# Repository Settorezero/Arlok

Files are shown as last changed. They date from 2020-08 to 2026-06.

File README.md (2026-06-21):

# Arlok

## Arduino Robot you can 3D-print it yourself!

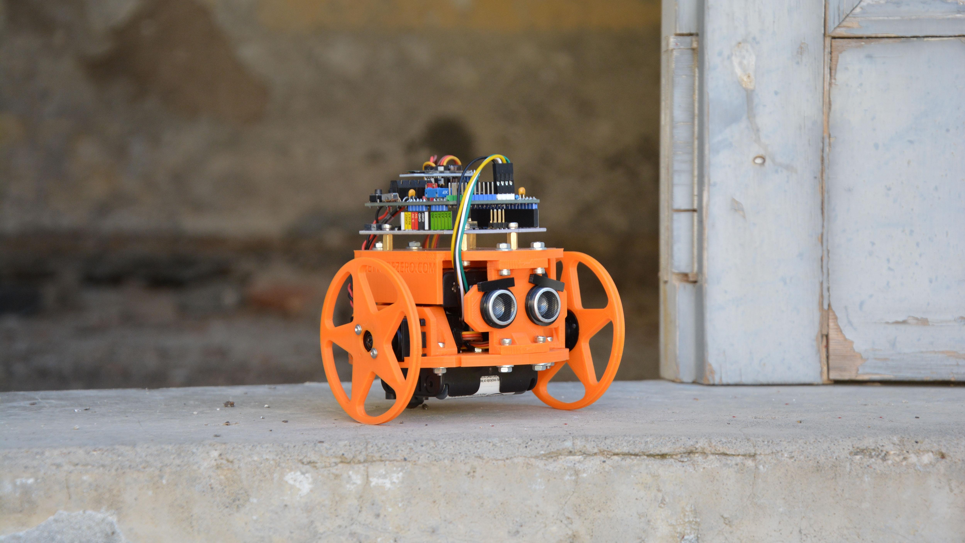
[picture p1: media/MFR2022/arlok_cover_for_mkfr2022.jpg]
Arlok - Maker Faire 2022


Arlok is a simple educational Robot based on Arduino Uno with parts printed in 3D and all easy-available components. 3D-printed parts are big, easy to manipulate and printed even by cheap 3D-printers. Arlok is highly customizable: you can change wheels and tires, supports, powering systems and give Arlok an expression too! Arlok is cheap, cute and easy to assemble and program. There are some programming examples that will make this robot moving around avoiding obstacles, following a line on the floor or let you control it using your cellphone with an Android app (source code of app provided too!).  

## What you need for build an Arlok

- Bill Of Materials: [[:uk: ENG](./docs/BOM.md)]   [[:it: ITA](./docs/BOM_ita.md)] 
- [3D-printed parts (version 1)](./cad/v1)
- [3D-printed parts (version 2 - still preliminary)](./cad/v2)

Please note: version 1 and version 2 parts are not compatible each other!  

## Version 1 vs Version 2

First Arlok version is from 2020: it was designed during Covid-19 pandemy (the very first version of the robot was called AR.L.O.). At ther time I used Tinkercad that allowed me to teach something new to my sons during the lockdown. In 2024 I started to design a new version using OnShape by PTC, mantaining the same concept design and adding some features such like a battery display and a new kind of ball-caster, but the 3D printer I had at time didn't allowed me to make some things I had in my mind. In 2025 I bought a new 3D-printer so I started to design the new version more seriously. Version 2 is here but is still a preliminary version: I added the final STEP and STL files but actually I hadn't much time for writing an assemblying tutorial like I done for the first ARLOK revision.  

Differencies between version 1 and version 2:

- The Tamiya 70144 ball-caster is no longer needed: I designed a foot for using a classic 2.5x4.5 furniture ball-caster you can find on Amazon: [sponsored link](https://amzn.to/42y9IiS). Anyway the Tamiya Ball-Caster can be used if you already have it but you must print a simple adapter you can find in both stl and step folders
- Wheels are slightly bigger and larger and are made for using only TPU printed tires: so no o-rings are needed but you need to know how to properly print TPU on your 3D-printer
- Different design for all parts: sonar and switch pillars now are larger and they cover the empty spaces giving a cleaner appearance
- Redesigned the whole chassis with the usage of a single 18650 LiPo cell in mind so, in the V2 there is no room for AA-size battery holders
- Added the possibility to use 2 18650 in parallel using the bracket for dual batteries
- Added an 1S battery display on a side
- Added a proper placement for the TP4056 (protected) 1S battery charger (tested both micro-usb and usb-c types)
- Added a proper placement for the SX1308 boost converter
- Added placement for an XL6009 boost converter (also for the XL6019 but this one cannot be used since it requires an higher input voltage, 5V)
- Added the possibility to use an VL53L0X TOF sensor instead of ultrasonic one
- Changed dimensions for allowing to use screws that will not pop-up from panels
- Changed placement of some parts for giving Arlok more stability
- Added groves for embedding nuts in some points
- Added holes and slots in certain points for passing cables in a cleaner way
- Added vent-holes for servos and boost converters
- Added handles on top for carrying Arlok more safely
- Added a further plate on top of the handles for having more expansion possibilities: plates allows the positioning of a 400-points breadboard (82x55 like this: [sponsored link](https://amzn.to/4uJOeeZ))
- Added a pedestal: you can leave Arlok on top of this pedestal for making maintenance/tuning/upgrade or simpy for showing it or allowing it to rest...

## Assembling

The Version 1 has a step-by-step guide assembly guide: [[:uk: ENG](./docs/assembly_v1.md)] - [[:it: ITA](./docs/assembly_ita_v1.md)]  
The Version 2 still doesn't have an assembly guide

## Code examples

See in the [Arduino folder](./arduino) for code examples or write your own code using one of the provided example as base!

## Mods and Upgrades

- Powering Arlok V1 from a LiPo Battery: [[:uk: ENG](./docs/lipo_mod.md)]  [[:it: ITA](./docs/lipo_mod_ita.md)] (Arlok V2 can be only powered from a LiPo)
- Hacking an analog servo for continuous rotation: [[:uk: ENG](./docs/servo_mod.md)]  [[:it: ITA](./docs/servo_mod_ita.md)]

## Troubleshooting

[Troubleshooting guide](./docs/troubleshooting.md)  

## Links

- [Greta Galli review](https://www.youtube.com/watch?v=CbPGWd9I_mA)

- [Dario Ciceri review](https://youtu.be/yjnFxoAIeAM?list=LL&t=208)

- [Aperitech about ARLO (first ARLOK rev)](https://www.youtube.com/watch?v=JS_QYEIMfNo)

- [All ARLOK videos on Youtube](https://tinyurl.com/arlokplaylist) 

- ARLOK on no. 253 (2021) of Italian Magazine "Elettronica IN": [EXCERPT](https://www.elettronicain.it/wp-content/uploads/prog_copertina/arlook_il_robot_per_tutti.pdf) -   [MAGAZINE ISSUE](https://www.elettronicain.it/prodotto/n-253-aprile-2021/?tracking=5f004a6ba8be7)

- Maker Faire 2022 [Interview by "uno scemo qualunque"](https://www.youtube.com/watch?v=RNEsY1jSlT4&t=576s)

- ARLOK partecipated to the 2020 Maker Faire European Edition (Project 253, Stand E57) - with Officine Robotiche

- ARLOK partecipated to the 2022 Maker Faire European Edition (Project 93, Pavillon D19) - with Pizza Robotics

- ARLOK partecipated to the 2023 Maker Faire European Edition (Project E62, Pavillon 5, Booth D6) - with Pizza Robotics

- ARLOK v2 partecipated to the [2026 Maker Faire Caserta](https://caserta.makerfaire.com/maker/entry/12/) (Project 12, Stand D7)

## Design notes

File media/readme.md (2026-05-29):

# Arlok (v1) Images and Renderings

- [Assembly](arlok_3d_view.stl)
- [Exploded View](arlok_3d_exploded.stl)
- [Arlok Press High Res Pictures](https://photos.app.goo.gl/kQAZxSGqNprd3ggg6)

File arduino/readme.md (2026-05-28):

# Arlok Source Code for Arduino IDE

This folder contains Arduino sketches to be used with [Arduino IDE](https://www.arduino.cc/en/main/software) after installing libraries showed in the next paragraph

> Note: The [motors setup procedure](motors_setup.md) it's only implemented in the `explorer` and `explorer lipo` sketches.

## Libraries

You'll need the following libraries installable directly from Arduino IDE otherwise specified

- [Adafruit SSD1306](https://github.com/adafruit/Adafruit_SSD1306)
- [Adafruit GFX](https://github.com/adafruit/Adafruit-GFX-Library)
- [TimerOne](https://github.com/PaulStoffregen/TimerOne) 
- [Servo Timer 2](https://github.com/nabontra/ServoTimer2) - (manual install)
- [VL53L0XV2 by Pololu](https://github.com/pololu/vl53l0x-arduino)
- [U8G2](https://github.com/olikraus/u8g2)
- [Huskylens](https://github.com/HuskyLens/HUSKYLENSArduino/tree/master) - (manual install)

## Arduino IDE Setup

Even if you're using the [MakerUNO](https://makeruno.com.my/) or other Arduino UNO compatible boards, simply select _Arduino UNO_ from the board manager. Then select the correct COM port.

## Code examples

- [Explorer](./01_Explorer) : Arlok moves around avoiding obstacles detected with ultrasonic sensor
- [Explorer TOF](./02_Explorer_TOF) : Arlok moves around avoiding obstacles detected with a VL53L0XV2 TOF Sensor (requires the V2 chassis)
- [Line Follower](./03_Linefollower) : Arlok moves following a line painted on the ground
- [Bluetooth Remote](./04_Bluetooth_Remote) : You move Arlok using Bluetooth Classic with an Android phone. Source code for Android app provided too
- [Huskyklens](./05_Huskylens) : Arlok will follow a face using an Huskylens from DFRobot

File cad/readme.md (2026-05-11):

# Arlok Files for 3D printing

- [V1](./v1) folder contains version 1 files, designed with thinkercad
- [V2](./v2) folder contains version 2 files, designed with onshape. This is still a preliminary version

PLEASE NOTE: version 1 and version 2 are not compatible each other since they've different dimensions!

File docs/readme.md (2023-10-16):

## Arlok Documents  

In this folder are contained useful documents for working with ARLOK Arduino Robot.

- [Bill of Materials](BOM.md)
- Assembly instructions: [ENG](assembly.md) - [ITA](assembly_ita.md)
- How to hack Servo for continuous rotation: [ENG](servo_mod.md) - [ITA](servo_mod_ita.md)
- [Connection table](connections.md)
- [Arlok shield schematic](arlok_schematic_rev1.png)
- Different ways to powering Arlok : [ENG](powering.md)
- Mod: Powering from a LiPo Battery: [ENG](lipo_mod.md) - [ITA](lipo_mod_ita.md)

Datasheets and manuals from product manufacturers (folder datasheet)
- [Maker UNO schematic](schematic_maker_uno.pdf)
- [Maker Line datasheet](makerline.pdf)
- [Arduino UNO schematic (only for reference)](schematic_arduino_uno.pdf)
- [HC-06 Bluetooth Module manual](HC-06_manual.pdf)
- [HC-05 AT commands](HC-05_AT_commands.pdf)
- [HC-05/06 module series](HC-0x_module_series.pdf)

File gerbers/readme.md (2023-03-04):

# Arlok PCB Gerbers (REV 1)
  
This folder contains gerber files for lastest version (REV1) PCB manufacturing. You can preview them using a free Gerber Viewer such as [GerbV](http://gerbv.geda-project.org/).  
I advice you to let PCBWay make the PCBs for you since they already have those files, without the need for you to upload and set an order.

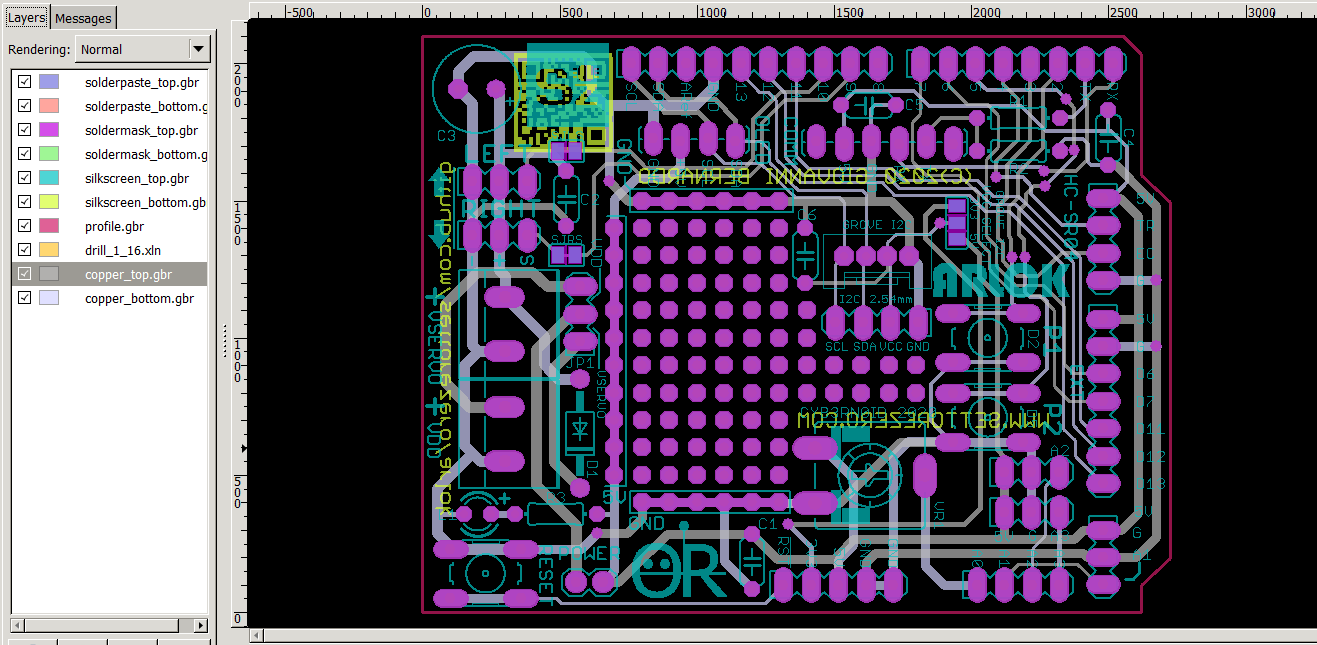
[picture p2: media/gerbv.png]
ARLOK Gerbers in GerbV


## How make ARLOK REV1 PCBs on PCBWay

- Register to PCBWay using [my refferer link](https://www.pcbway.com/setinvite.aspx?inviteid=355653&from=settorezero2020)
- Upon you registered, go to the [PCBWay ARLOK shared project page](https://www.pcbway.com/project/shareproject/ARLOK_Arduino_Shield_Rev_1_ad0b448d.html)
- Click on "Add to Cart" button on the right
- A pop-up will show up: all default settings are good. You must only select how many PCBs you want: the minimum quantity, by default, is 5. The first order of 5 PCBs is free on PCBWay: you must pay only the shipping costs

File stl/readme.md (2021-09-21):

# Arlok 3D Files for 3d-Printing 
This folder contains parts to be 3D-printed.  I like to use the [Sunlu PLA+](https://amzn.to/3aG5V7i) filament.  
> Quick link to this page: [https://tinyurl.com/3dprintarlok](https://tinyurl.com/3dprintarlok)  

## Summary
+ [Printer settings](#printersettings)
+ [Main Parts](#mainparts) 
+ [Main Parts description and notes](#descriptions)
   1. [Plate bottom](#platebottom)
   2. [Plate top](#platetop)
   3. [Servo brackets](#servobrackets)
   4. [Sonar pillar](#sonarpillar)
   5. [Rear pillar](#rearpillar)
   6. [Wheels](#wheels)
   7. [Tires](#tires)
   8. [Via Pixetto support](#viapixetto)
   9. [18650 cell bracket](#18650)
+ [How customize the wheels](#customizewheels) 
+ [Moods](#moods)

## Printer settings
Values in the parts table are calculated using CURA slicer with following settings:

- Layer Height: 0.2mm
- Top Layers: 5
- Bottom Layers: 5
- Wall line count: 3
- Print speed: 30mm/sec
- Infill speed: 50mm/sec
- Travel speed: 65mm/sec
- Infill density: 20%
- Generate Support: NO
- Build plate adhesion type: skirt

I use those slow settings because I've a cheap 3D-Printer and I need to print slow. Also Infill maybe is slightly oversized since pieces are pretty big. If you've a good 3D-printer you can speed-up and lower the infill.

## Main Parts
You can see the [Arlok Exploded View](../media/arlok_3d_exploded.stl) for seeing how parts must be assembled.  
Part quantity in parenthesis indicates that this is an optional or an alternative part.  
Time and weight is reported for total parts if more than one is needed.

| Qt. | File | Print Time (minutes) | Weight (grams)| Notes |
|-----|---|---|---|---|
|  1  | [Plate Bottom](arlok_plate_bottom.stl) | 199 | 26 |  |
|  1  | [Plate Top](arlok_plate_top.stl) | 216 | 30 |  |
|  2  | [Servo Bracket](arlok_servo_bracket.stl) | 106 | 12 |  |
|  1  | [Sonar Pillar](arlok_pillar_sonar.stl) |  48 |  6 |  |
| (1) | [Sonar Pillar (round variant)](arlok_pillar_sonar_(variant_rounded).stl) |  48 |  6 |  |
| (1) | [6mm hole Rear Pillar](arlok_pillar_hole_(variant_06mm).stl) |  40 |  6 |  | 
|  1  | [10mm hole Rear Pillar](arlok_pillar_hole_(variant_10mm).stl) |  40 |  5 |  |
| (1) | [12mm hole Rear Pillar](arlok_pillar_hole_(variant_12mm).stl) |  40 |  5 |  |
|  2  | [Wheel](arlok_wheel.stl) | 178 | 28 |  |
| (2) | [Wheel - slotted holes](./wheels/arlok_wheel_slotted.stl) | | |  |
| (2) | [Wheel - 5-star](./wheels/arlok_wheel_star5.stl) | | |  |
| (2) | [Wheel - 10-star](./wheels/arlok_wheel_star10.stl) | | |  |
| (2) | [Wheel - honeycomb](./wheels/arlok_wheel_honeycomb.stl) | | |  |
| (2) | [Wheel - circles](./wheels/arlok_wheel_circles.stl) | | |  |
| (2) | [Wheel - snowflake](./wheels/arlok_wheel_snowflake.stl) | | |  |
| (2) | [Tire - round profile](./tires/arlok_tire_round.stl) | | | See descriptions |
| (2) | [Tire - flat profile](./tires/arlok_tire_flat.stl) | | |  |
| (2) | [Tire - knurled](./tires/arlok_tire_knurled.stl) | | |  |
| (1) | [Via Pixetto Support](arlok_via_pixetto_support.stl) |  53 |  6 |  |
| (1) | [18650 LiPo Holder](arlok_18650_holder.stl) | | |  |
| ( ) | [Moods](./moods/) | | |  |

Estimated total printing time for standard parts: 13H 7'  
Estimated total filament needed for standard parts: 107g (about 36meters)

## Main Parts description and notes

### Plate Bottom
Front side is the one with the arrow on top. On front side there are two slotted holes: they are used, eventually, for attaching the Cytron Makerline module used for the line follower example. Servos must be mounted on top placing them in the grooves and having the shaft towards the front.

### Plate Top
You'll mount the Maker UNO board on top using 4 8mm or 10mm spacers. The two lateral wings will hold the 4AA battery holder in place.

### Servo Brackets
Bracket to hold in place the 2 servos: there is no need to attach servo to the bracket with screws even there are holes (they're placed there only for reference).

### Sonar Pillar
There are 2 variants: the standard, having squared edges, and the one with rounded edges, print only one of these.

### Rear Pillar
There are 3 variants that differs for the hole diameter used for the switch that detaches the 4AA batteries of the servo power. Print only 1 of these. 6mm variant will be used for the classic lever switch. 10mm variant is used for the 10mm lock pushbuttons. 12mm variant is used for the 12mm lock pushbuttons sold by FuturaShop (see [BOM in the docs folder](../docs/BOM.md)).

### Wheels
There are various kind of wheels optimized to be used with the round horn that comes with the MG996R servo and for an O-ring (or provided tires to be 3D-printed) having an internal diameter of 70mm and a section of about 2 or 3mm. Wheels are sized for giving the correct balance of the robot using the Tamiya 70144 ball caster mounted in the 25mm variant. The wheels will be attached to the servo Horns using 2 self-tapping screws given with the servos. A rubber O-Ring or a provided tire (3D printed using a flexible material like TPU) will be applied to the wheel groove for giving grip. 

The are:  
- The first, original [Wheel](./wheels/arlok_wheel.stl), see the [How customize the standard wheel](#customizewheels) for further informations
- [Wheel - slotted holes](./wheels/arlok_wheel_slotted.stl) designed by @gbr1 ([picture](../media/misc/wheel_slotted.jpg))
- [wheel - 5-star pattern](./wheels/arlok_wheel_star5.stl) designed by @gbr1
- [wheel - 10-star pattern](./wheels/arlok_wheel_star10.stl) designed by @gbr1
- [Wheel - honeycomb pattern](./wheels/arlok_wheel_honeycomb.stl) designed by @gbr1
- [Wheel - circles](./wheels/arlok_wheel_circles.stl)
- [Wheel - snowflake](./wheels/arlok_wheel_snowflake.stl)

### <a name="tires">Tires
You can use an O-ring having an internal diameter of 70mm and a section of about 2 or 3mm or, if your printer can handle flexible filaments (like TPU), you can print one of those provided tires: 

- [Tire - round profile](./tires/arlok_tire_round.stl) designed by @rbonghi (picture [[1]](../media/misc/tire_round_01.jpg) [[2]](../media/misc/tire_round_02.jpg))
- [Tire - flat profile](./tires/arlok_tire_flat.stl) designed by @gbr1
- [Tire - knurled](./tires/arlok_tire_knurled-stl) designed by @Dario-Ciceri

>@rbonghi advices those settings for the tire:
>- Filament: TPU SainSmart
>- Infill Density: 5%
>- Infill pattern: Honeycomb
>- Retraction: Disabled
>- Temperature Nozzle: 235 - 230
>- Temperature Bed: 45 - 40

###  Via Pixetto support
This support is used for attaching a [Via Pixetto Ai Camera](https://pixetto.ai/) on top-front of Arlok. The support is a hinge made of 2 pieces: you must use a long M3 screw and a nut. In the STL there are also 4 small spacers used for distancing the camera from the base: you must use M2 screws and nuts. Sorry but Via Pixetto example is still not ready.

###  18650 LiPo Holder
This part is used for holding a 18650 cell battery on the bottom of the robot. The 18650 will be used alone, without the two AA battery holders. You can use a single 18650 attached to a DC/DC boost converter through the pushbutton switch mounted on the rear pillar. Use a 18650 having soldering tabs. 

>**!!! WARNING !!!**  
**LiPo batteries can be very dangerous so don't mount this kind of battery if Arlok will be used by a child!**
  
I've successfully used a 2A DC/DC boost converter based on the [SX1308](https://amzn.to/3y07eIX). Set the converter for giving 6V at output, then feed the 6V in the `VSERVO` screw terminal and put the `JP1` jumper in `VSERVO` position and leave ON the `POWER` jumper/switch on the PCB: the main power will be disconnected through the pushbutton on the rear pillar.  

The LiPo must not go under a certain voltage so you can feed the positive terminal of the LiPo battery directly in one free analog input (`A2` for example) for checking the battery voltage and stop the robot if voltage goes below 3.2V.  
  
With those modifications the logic will be powered at about 5.3V (the 6V from the boost converter will be scaled down of about 0.7V by the voltage drop caused by `D1` diode), so for checking analog voltages keep in mind that the value `1023` from the ADC will be equal to about 5.3V (measure the precise voltage on the 5V pads and make computations accordly).  
  
This picture shows how 18650 will be mounted on the bottom of Arlok (use 2x M3 12mm screws, 2x M3 nuts and 2x M3 washers):

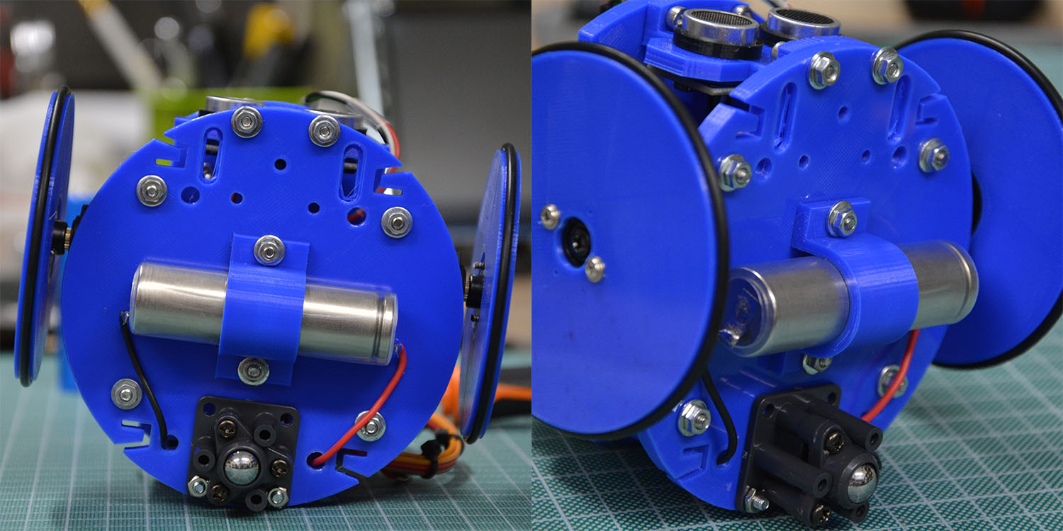
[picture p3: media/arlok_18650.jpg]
18650 LiPo battery mounting


For recharing the battery you can use a cheap module for LiPo Charging having battery protection (mandatory!), such as [this kind of module](https://amzn.to/3qjoea8) based on the `TP4056`. Module with protection are slightly larger of the ones without protection and have an additional IC on top: so be sure to buy the type having protection! It's not adviced include the battery charged on the robot: better solder two wires with crocodile-clamps on charging module and attach it to battery tabs having care robot is turned off.
  
The SX1308 module will be placed inside the robot since there is a lot of space where the 4xAA battery holder would be.  
   
If you experience some problems like reset of the Arduino, you can increase the `C3` value. If you experience bluetooth module reset, increase the value of C5 or put an electrolytic capacitor (mind the polarity in this case!).

Anyway this setting is still experimental, was not tested under all conditions.

## How customize the standard wheel
Wheels are generated with [Openscad](https://www.openscad.org/) using [Obijuan script](https://www.thingiverse.com/thing:19940) of the Servo Wheel on Thingiverse. You can found the script also on his [Github Repo for Miniskybot](https://github.com/Obijuan/Miniskybot/).   

Customizing wheel is useful only if you plan to use a different ball-caster that gives the robot a different clearance from the floor.  

In the Obijuan script you can customize all wheel parameters. I've generated the default wheels using following measures:  
- external (finished) diameter: 75mm
- height: 5mm
- horn diameter: 21mm. 

See the following image for understanding servo parameters in the openscad script:  

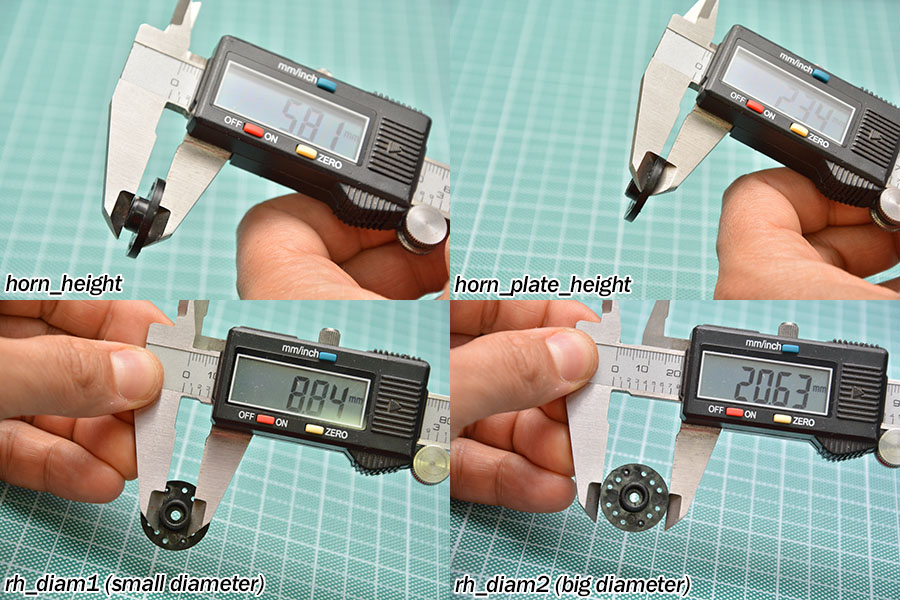
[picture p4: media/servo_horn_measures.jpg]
Servo Horn measures


## Arlok Moods

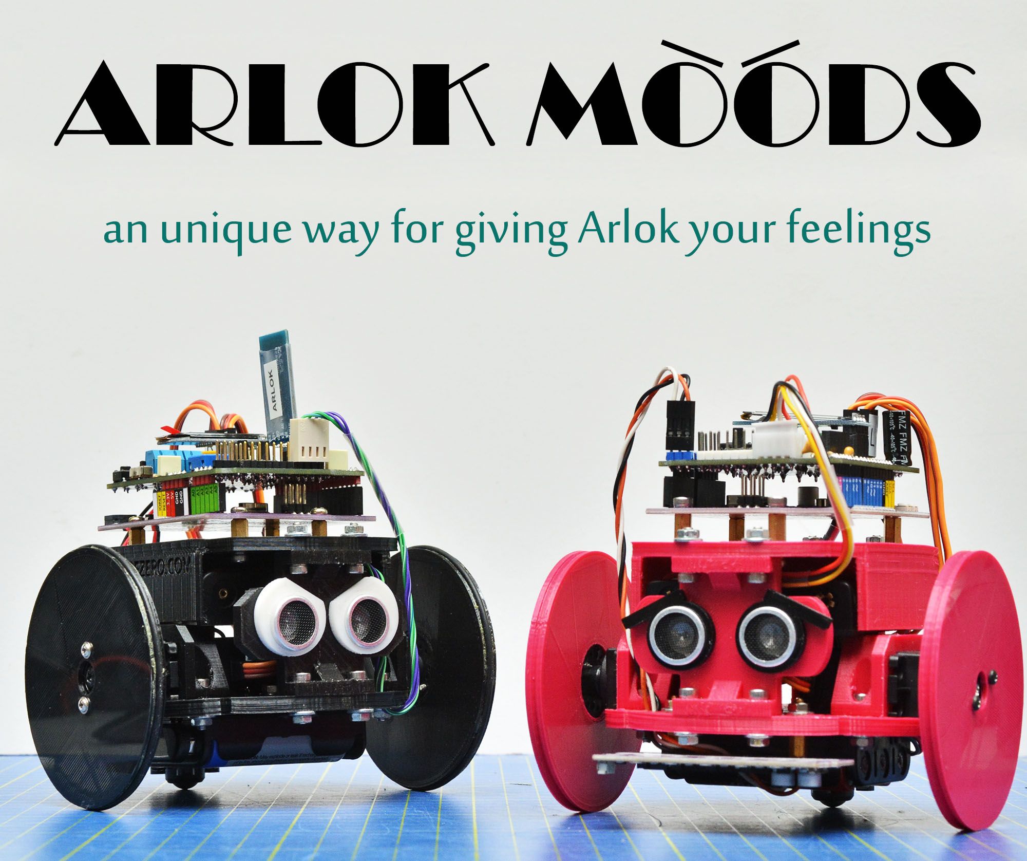
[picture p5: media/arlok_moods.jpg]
Arlok moods


_Arlok Moods_ was introduced first time along the Arlok first release with the only eyelashes for _Arlokka_. Now we've included a lot of other moods: they are very small parts to be 3D printed and attached on ultrasonic capsules for giving your Arlok an unique expression.   
  
Those parts are very useful also for keeping ultrasonic sensor in place. You can also combine different Arlok moods and attach up to 2 moods for each capsule: but in this case is better glue them together.

| File | Description | Colors adviced |
|---|---|---|
| [Eyelashes](./moods/mood_eyelashes.stl) | Long eyelashes for giving Arlok a female or fashion aspect | Black, Gold, Copper, Silver, White |
| [Eyebrows](./moods/mood_eyebrows.stl) | You may give Arlok a bad or sad expression by tilting those eyebrows | Black, Gold, Copper, Silver, White |
| [Thick Eyebrows](./moods/mood_eyebrows_thick.stl) | Bigger centered eyebrows for make Arlok look unibrowed or to be used in combination with one above eyebrow for looking perplexed| Black | 
| [Cartoon](./moods/mood_cartoon.stl) | Print them in white color: they will give Arlok eyes like a cartoon. Print them in red color for making Arlok looks mad. | White, Red, Yellow, Lime |
| [Cartoon with eyebrows](./moods/mood_cartoon_eyebrows.stl) | As above but with a cut for giving bad/sad expression. |  White, Red, Yellow, Lime |
| [None](./moods/mood_none.stl) | Simple round discs for no expression and keeping capsules in place. Try to print them in a different color than chassis | Any |
| [Meme "Feel like a sir" - Hat](./moods/mood_sir_hat.stl) | Hat from "Feel like a sir" meme | Black |
| [Meme "Feel like a sir" - Monocle](./moods/mood_sir_monocle.stl) | Monocle from "Feel like a sir" meme | Golden/Black |
| [Meme "Feel like a sir" - Moustache](./moods/mood_sir_moustache.stl) | Moustache from "Feel like a sir" meme | Black |

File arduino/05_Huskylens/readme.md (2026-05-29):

## Huskylens demo

I'm using the first Huskylens model ([SEN0305](https://wiki.dfrobot.com/sen0305/)) in this example, not the new (2) version. In order to make this demo working I made two puppets having the face of *Hide The Pain Harold* and *Mr. Bean* : I printed the face on paper using the printer and I attached them to a Maker Faire Puppet. I prepared a PDF with faces to print in a 2D paper printer and all other parts: this stuff along some instructions, is contained in the [props](props/) folder here.  

I programmed the Huskylens for detecting the face of *Hide The Pain Harold* as `ID1` and *Mr. Bean* as `ID2`. I'll show you how to do this. In the Arduino Code I will make Arlok moving by following only *Harold* even if it can recognize *Mr Bean*.  

## Libraries

In this example I used the **U8G2** library for the OLED display instead of the _Adafruit_SSD1306_. You can install the U8G2 library directly from Arduino IDE.  

You must install the Huskylens library manually: unfortunately is not available for installing it directly from Arduino IDE. I'll show you how to do it the simple way:

First Download the whole [Huskylens Repository](https://github.com/HuskyLens/HUSKYLENSArduino/tree/master) by clicking on the 'Code' button and then 'Download ZIP':

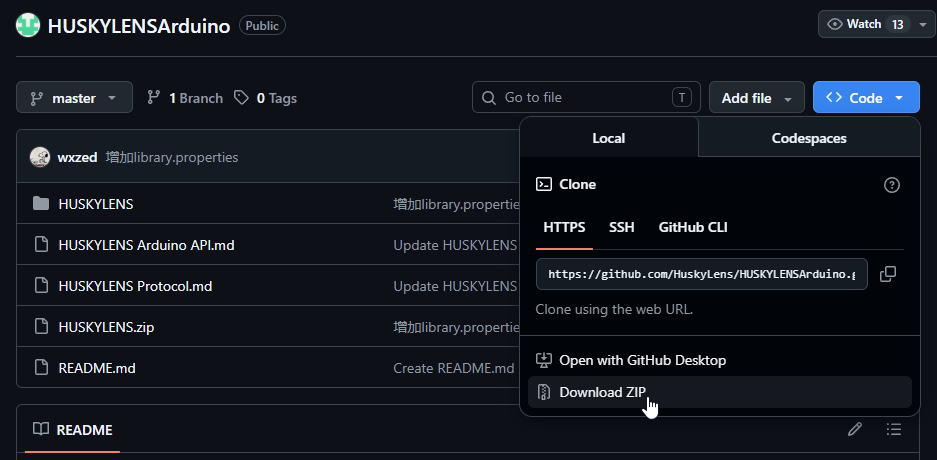
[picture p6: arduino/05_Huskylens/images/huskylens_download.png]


You will obtain a file called _HUSKYLENSArduino-master.zip_. Extract the ZIP file. Once extracted you'll notice there is a further _HUSKILENS.zip_ file : leave it as is (don't extract it!). 

Open Arduino IDE. Click _Sketch -> Include Library -> Add library from a zip file_:

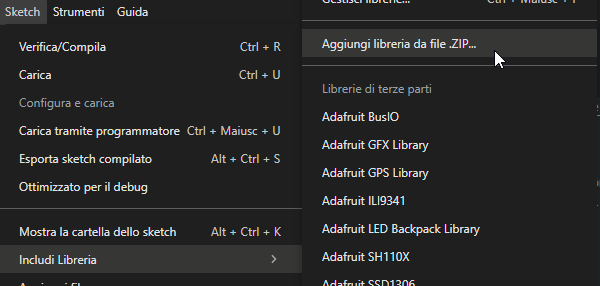
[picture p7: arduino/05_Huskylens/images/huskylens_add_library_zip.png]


Now point to the _HUSKILENS.zip_ file you obtained previously:

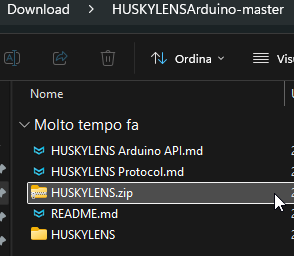
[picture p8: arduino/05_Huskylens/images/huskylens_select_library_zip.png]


All done! If you're working on Windows, you'll notice you've an _HUSKYLENS_ folder in the _Documents/Arduino/libraries_ folder.

## Huskylens Initial Configuration

Huskylens has to be configured for streaming data over I2C:

1) Power the Huskylens (I usually do this by connecting it via USB)
2) Turn the wheel to the right until you find `General Settings` and click the wheel
3) Go on `Protocol Type`, click the wheel
4) Select `I2C`. Click the wheel 
5) Turn the wheel to the left, click on `Save & Return` 
6) *Do you want to save data? YES*

Now the Huskylens will communicate through I2C : 

- Blue = SCL
- Green = SDA
- Red = +5V 
- Black = GND 

## Program the Huskylens for detecting multiple faces

We will use the *face recognition*: it works also with printed (2D) faces. We will program it for detecting more than one face and we will use puppets contained in the [props](props/) folder.

> Note 1: When nothing is learned (Huskylens is not programmed for recognizing something) a small cross appears at center of the display. In other words: when you see the cross at display center, means Huskylens is not programmed for detecting objects.

> Note 2: If cross doesn't appear, and then Huskylens is programmed for detecting some object(s), and you want to remove this program: click the button on the right of the Huskylens (not the wheel, but the button on the opposite side): a writing `Click again to forget` appears. If you click the right button again, first the countdown reaches 0, you'll delete actual objects learned.

1) Use the wheel for going to `Face Recognition`
2) Click the wheel for select this mode
3) Click the wheel again and keep it pressed: this action will enter the setup menu for the current selected mode
4) Move the wheel and select `Learn Multiple`: a slider appears for activating this mode: move it to the right and click the wheel
5) Move wheel to the left and select `Save & Return`
6) *Do you want to save Data? Yes*
7) Put the face you want to save as first ID in front of camera, having the cross at center of the face. Be sure there is proper illumination. We will use the "Hide The Pain Harold" face as first ID
8) A white square (called _bounding box_) will appear around the face with the `face` writing on top
9) Click the right button to save this face. Now, first than countdown reaches zero, press again the right button to learn the second face
10) The first learned face now has a blue bounding box and the `ID:1` writing
11) Put the second face in front of camera and press the right button
12) You can continue to making Huskylens learn other faces following this method
13) After you pressed the right button for storing the last face, let the countdown go to zero to exit

The name to a face ID can be assigned only over serial at startup and is not stored in the Huskylens: the example program does this.
  
Every face/object recognized from the camera will produce, over communication line, a string having X,Y value as the center of the bounding box, and W,H as Width and Height of the boundig box. Detecting X and Y we can know how the object is moving in front of camera (we will use only horizontal movement, X). Detecting Width and Height of the bounding box we can know if the object is near or far from camera (we will use only object width, W). Assuming a central position of the object, associated with a 'standard' width, we can assume object is far if the width detected id smaller than the 'standard' width.

## Powering

Huskylens draws about 900mA and it's necessary to have two separate power supply to function properly. I used two separate 18650 LiPo, each one having his own TP4056 (protected) for charging and a boost module. This is the schematic I made:

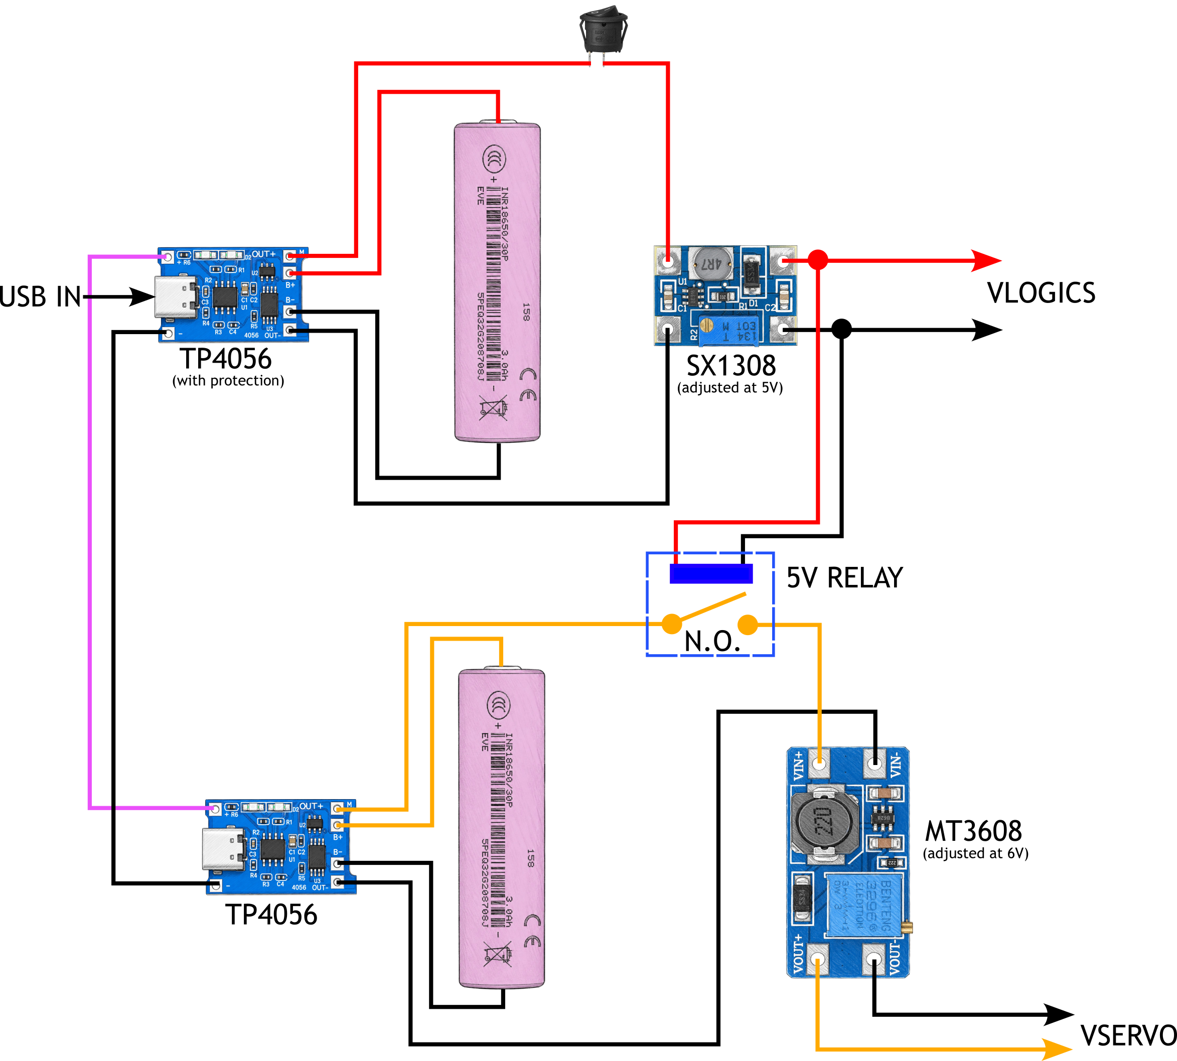
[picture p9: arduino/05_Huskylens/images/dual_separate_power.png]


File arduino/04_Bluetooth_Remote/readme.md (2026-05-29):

## Bluetooth Remote

Arlok is moved using an app on an Android device that sends serial commands over Bluetooth. For this example is needed an **HC-05** or an **HC-06** Bluetooth module. Android app + source code are provided here. 

Uncomment the row <kbd>#define LIPO</kbd> if you're using ARLOK powered from a LiPo Battery so you can read the battery voltage on the display. You can attach the positive lead of the battery to A2 pin for reading voltage, this pin is defined by <kbd>#define LIPO_PIN</kbd>.

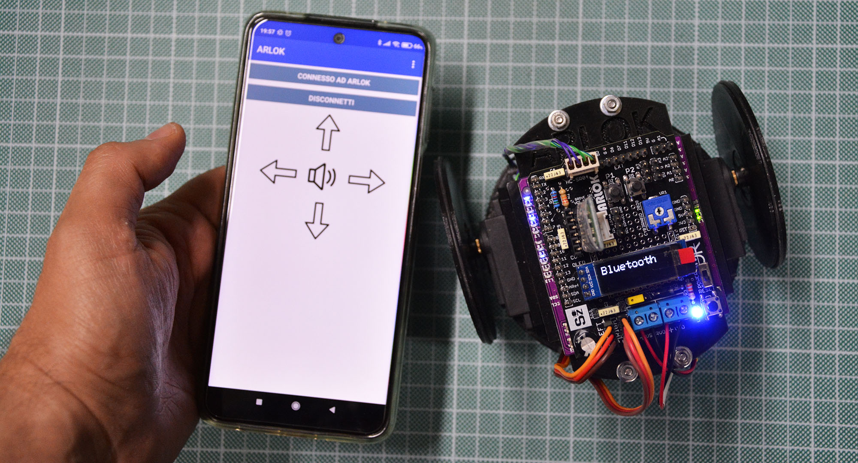
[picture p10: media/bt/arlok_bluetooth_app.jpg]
Arlok Bluetooth Remote App


### Motors Setup

See [motors setup procedure](../motors_setup.md)

## Bluetooth module attachment

Please pay attention to Bluetooth module attachment! Align `RX` of the module with `TX` on the silkscreen and so on. Usually module must go with chips and antenna toward the left side of the robot:

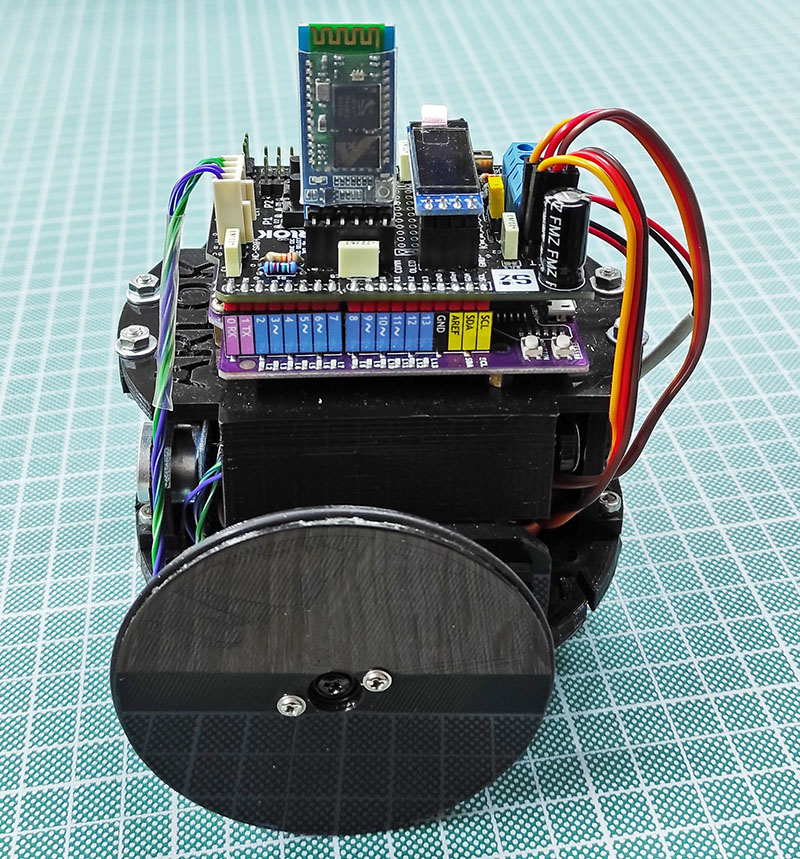
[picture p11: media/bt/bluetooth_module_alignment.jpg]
Bluetooth module alignment


Remember to detach the module while loading sketch on Arduino! Bluetooth module and Arduino Serial port share the same data line!

## Summary

1) [Differencies between Bluetooth Modules](#hc05vs06)
2) [Changing Bluetooh module name](#changename)
   1) [on HC-05](#hc05name)
   2) [on HC-06](#hc06name)
3) [Pairing module to the phone](#pair)
4) [Upload the code](#code)
5) [Use the ARLOK App](#app)
6) [Use Bluetooth Electronics](#kwl)

###  Differencies between HC-05 and HC-06

Physical differencies between modules:  
  
- HC-05 has a button, HC-06 doesn't
- HC-05 is usually shipped with a 6-pin header, HC-06 is usually shipped with a 4-pin header

Things in which those module differs:
  
- On HC-05 for going in `AT` command mode, you must press the button on the module during the powering. HC-06 works always in `AT` mode. `AT` mode is used for giving configuration parameters
- The `AT` command mode baud rate of the HC-05 is **38400** while the normal mode works at **9600**. The HC-06 works always at **9600**
- HC-05 responds `OK` after sending `AT` string in AT mode for indicating the module is in AT mode. HC-06 does not respond to the simple `AT` command but requires full commands
- On HC-05, for setting the module name you must use `AT+NAME=[name]` while HC-06 don't want the `=` symbol: `AT+NAME[name]`
- HC-05 can work in Master or Slave mode (=default) giving an AT command, HC-06 is hardwired in slave mode. For ARLOK only slave mode is used, so you can use both modules.

###  Changing the Bluetooth module name

First Connect the bluetooth module (HC-0x where x=5 or 6) to an USB adapter capable to work at 3.3V : in this phase leave the USB adapter disconnected from the computer:  

- Connect HC-0x module Vcc to usb adapter +5V
- Connect HC-0x TX to USB adapter RX
- Connect HC-0x RX to USB adapter TX
- Connect HC-0x GND to USB adapter GND
- Set the USB module for working at 3.3V

> The HC-0x module need to be powered at 5V but TX/RX levels are at 3.3V. This is why you're connecting module VCC to 5V but you're setting your USB adapter for working at 3.3V

This image shows how an HC-05 module is connected to the [UART-I2C-SMBUS 2 USB adapter](https://www.settorezero.com/wordpress/bridge-da-uart-e-i2c-ad-usb/): 

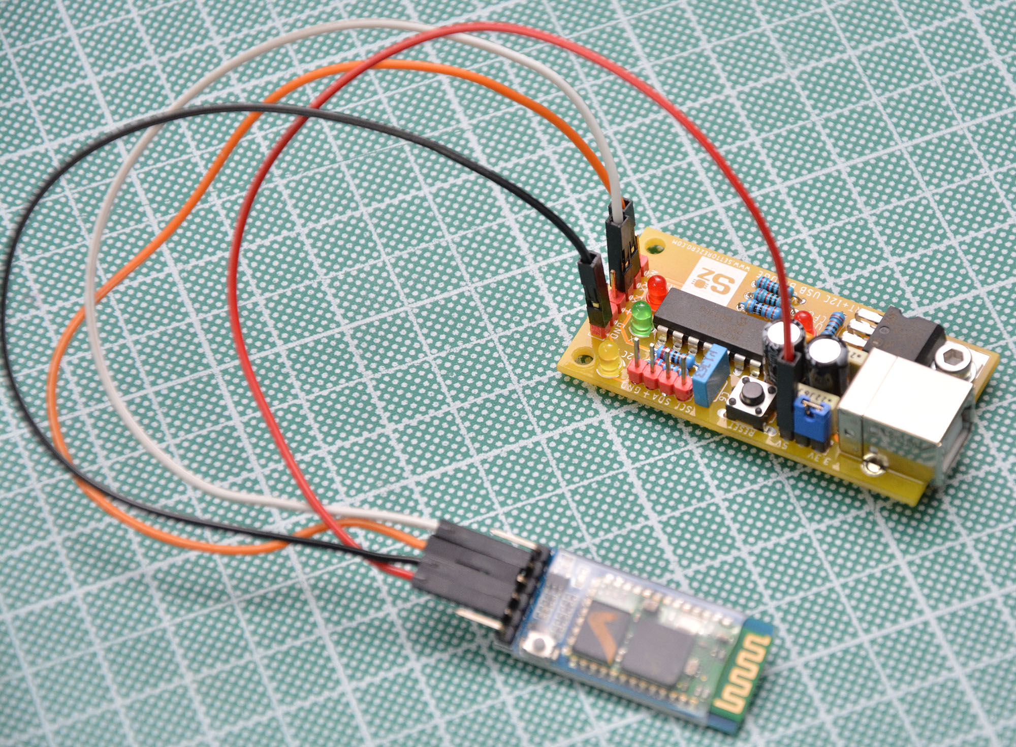
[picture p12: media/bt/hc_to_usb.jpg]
Module connected to USB adapter


If you use this module: put the power selection jumper in `3V3` position and use the remaining pin of this jumper for taking the 5V from USB for powering the bluetooth module (So, don't use the Vcc on the header).

####  Instructions for HC-05

On this bluetooth adapter, for entering `AT` mode you must press and keep pressed the button first than power the board. So press and keep pressed the button, then:  

- Connect the USB adapter to the computer
- The computer will recognize a COM port
- When red led starts to slowly flash, release the button
- Start a Serial Terminal program
- Be sure Terminal software appends `LF` and `CR` to the string. If those character are not appended, the module will not recognize commands!
- Choose the right COM port
- Set the baudrate to **38400**
- Open che connection to the COM port
- Send the string `AT+NAME=ARLOK`. The module will respond: `OK`

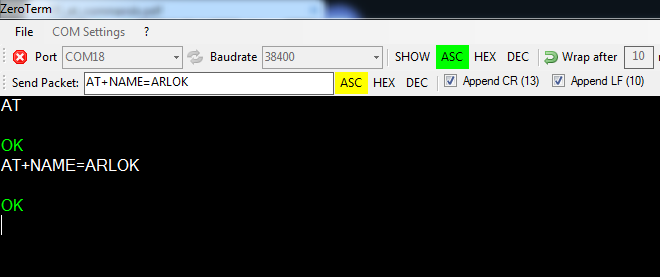
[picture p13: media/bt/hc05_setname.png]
HC-05 Set Name


- Close the connection
- Remove the power from the HC-05 Module

####  Instructions for HC-06

This bluetooh adapter works always in `AT` mode.

- Connect the USB adapter to the computer
- The computer will recognize a COM port
- Start a Serial Terminal program
- Be sure Terminal software appends `LF` and `CR` to the string. If those character are not appended, the module will not recognize commands!
- Choose the right COM port
- Set baudrate to **9600**
- Open che connection to the COM port
- Be sure Terminal software appends `LF` and `CR` to the string
- Send the string: `AT+NAMEARLOK`. The module will respond: `OKsetname`

HC-06 Set Name

- Close the connection
- Remove the power from the HC-06 Module

###  Pairing to the phone

Pairing is necessary since the module used are NOT BLE ones. So if you don't pair the module to your phone, Bluetooth apps will not work!

- Give power to the HC-0x Module
- Take a cellular phone and turn on the bluetooth
- Search for new bluetooth devices: `ARLOK` must appear in the list

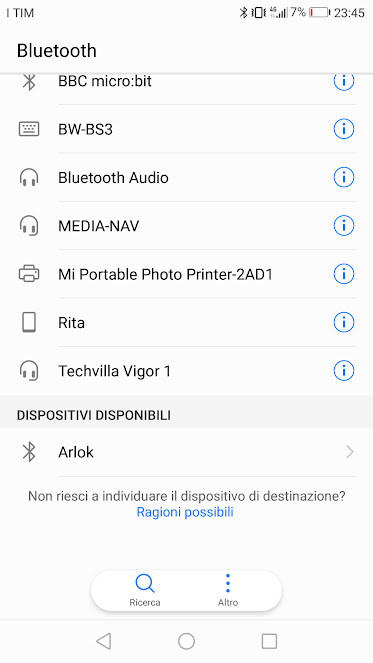
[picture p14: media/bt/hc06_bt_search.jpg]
HC-06 Bluetooth Search


- Select this device and associate it
- the default pin is **1234** (if does not work, try **0000**)

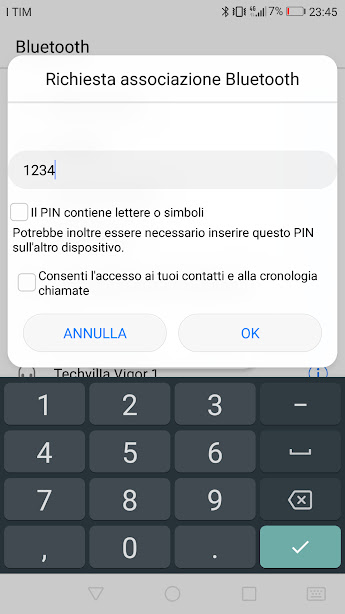
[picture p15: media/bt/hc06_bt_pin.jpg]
HC-06 Write Pin


First step is complete!

###  Upload the code

Code for Arduino is contained in the [bluetooth folder](./bluetooth).  

Pay attention: **Bluetooth module must be detached** from Arlok PCB when you connect the robot to the PC using the USB cable!  

Robot will receive commands in ASCII format:  

- 0 : motor stop
- 1 : move forward
- 2 : turn right
- 3 : move backward
- 4 : turn left
- Y : sounds the buzzer

You can use the ARLOK app on an Android phone for controlling it. Source code of the Android app is provided too.

###  Use the ARLOK App

In the [android folder](./android) is located the Android app made by Greta Galli. You must upload the `arlok.apk` file on your phone and install it.  
The `arlok.aia` is the source code of the app, made for Kodular.io.

###  Use Bluetooth Electronics

Here is a video showing this example: https://youtu.be/ISU3L3CCWP8

After you've paired the Bluetooth module with the phone, you can go further:  

- Install [Bluetooth Electronics by kewlsoft](https://play.google.com/store/apps/details?id=com.keuwl.arduinobluetooth)
- Open Bluetooth Electronics
- Some example panels are showed. When you select one, a Panel number with description is showed in the lower part of the screen.
- Select the first panel 
- Click on the save icon
- Click the button 'Load from Web Link'
- Delete the default text and write: https://www.settorezero.com/abt.kwl

> The kwl file is here too

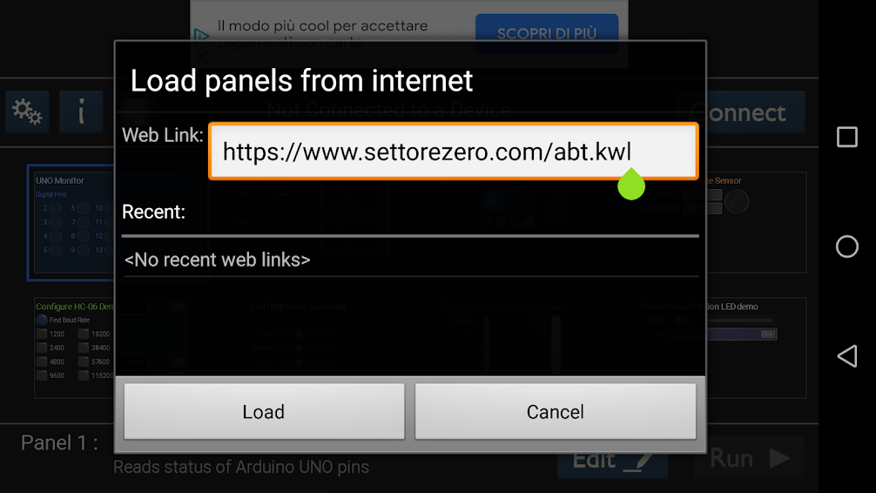
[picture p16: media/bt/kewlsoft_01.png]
Bluetooth Electronics - Load Arlok Panel


- Press Load
- A prompt "This will overwrite all panels!" will show: don't care, press OK
- An error will be showed: don't care
- The panel for this Arlok demo is showed in the first slot and all other slots are empty

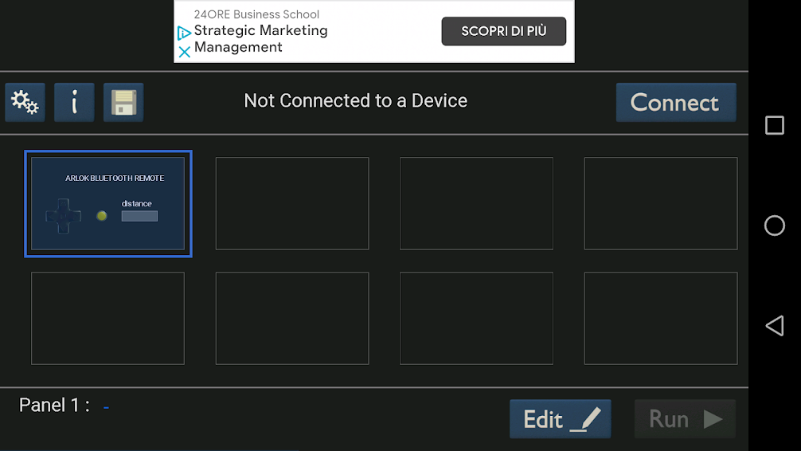
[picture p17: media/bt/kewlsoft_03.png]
Bluetooth Electronics - Arlok Panel Loaded


Note: for reset the previous panel click on the gears button and select 'Reset Default'. Previous panels will be reset and Arlok panel will be deleted

- In the Bluetooth Electronics panel clic the 'Connect' button
- Leave 'Bluetooth Classic' selected and press the 'Next' button
- In the paired device list, 'Arlok' must be present: Select it and press 'Connect'
- In the top screen 'Connected to: Arlok (followed my MAC address)' must be showed
- Press the 'Done' button
- Select the Arlok panel and pres the 'Run' button
- Move Arlok using the 4-way pad, sound the buzzer pressing the yellow button. The 'Distance' textbox shows the distance, expressed as cm, read by the sonar

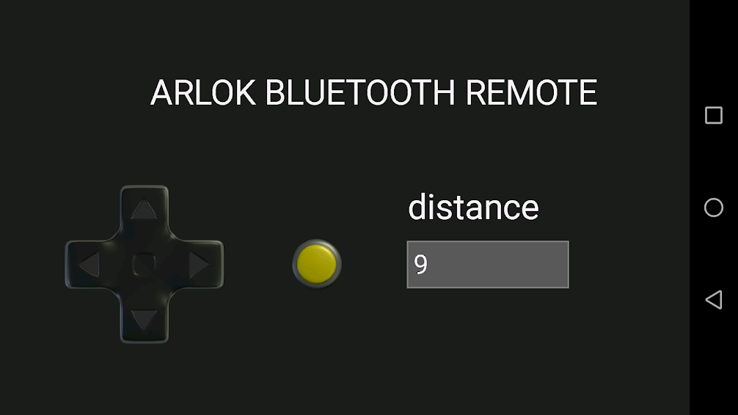
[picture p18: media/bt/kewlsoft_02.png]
Bluetooth Electronics - Arlok Panel Working


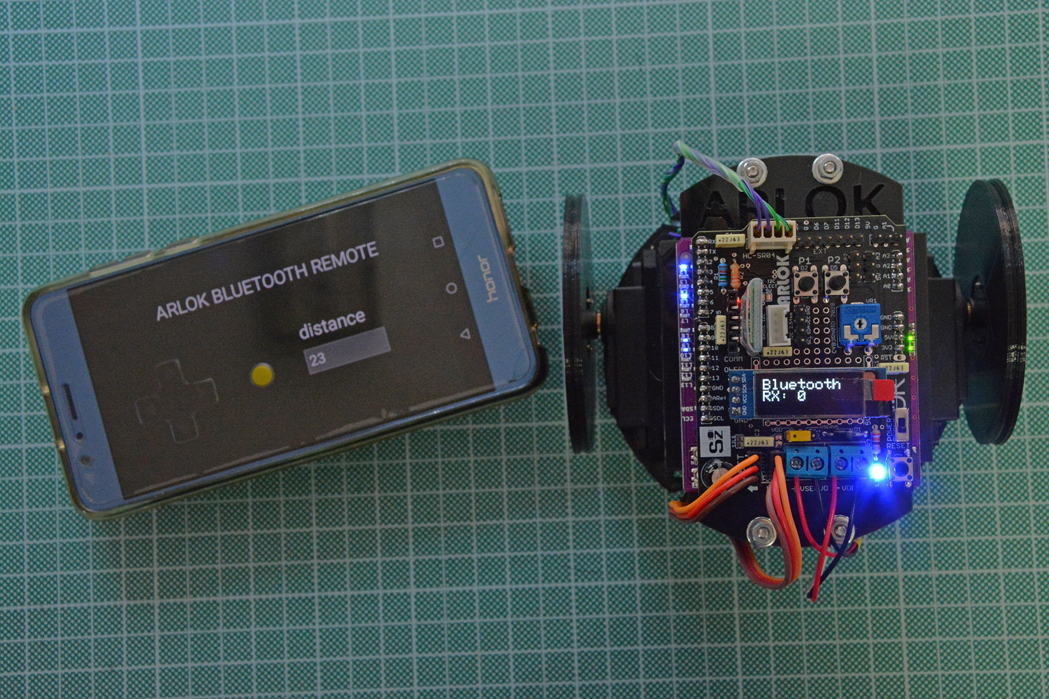
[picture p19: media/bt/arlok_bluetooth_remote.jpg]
Arlok Bluetooth Remote


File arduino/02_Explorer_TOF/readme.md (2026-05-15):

## Explorer TOF

Arlok moves forward, when he see an obstacle will make a sound (if you're using a MakerUno board), stop, move back, then turn random left or right and continue.  In this case a TOF sensor is used, model **VL53L0XV2**.

This sensor communicate over I2C: you can attach TOF sensor wires on I2C pad on top of the PCB (grove style or dupont). Close the jumper called "Grove I2C VCC select" between center pad and 5V for having 5V on both grove and dupont connector.

The TOF sensor will replace the ultrasonic one, you must print the <kbd>ArlokV2 - TOF Mask (single)</kbd> part for attaching the TOF sensor in front of Arlok: this part it's only compatible with the V2 chassis version.

For using the TOF sensor you must install the VL53L0X library by Pololu (tested the 1.3.1 version).

Uncomment the row <kbd>#define LIPO</kbd> if you're using a 18650 and you want to show the battery voltage on the display second Row: in this case connect the positive pole of the battery (after the power switch) directly to the pin A2: this pin is defined by <kbd>#define LIPO_PIN</kbd>.

### Motors Setup

See [motors setup procedure](../motors_setup.md)

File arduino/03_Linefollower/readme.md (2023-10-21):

## Line Follower

The _Line Follower_ is a Robot that must be able to follow a line, usually white on a black background or black on a white background, so that the difference between the two colors is clear and easier to identify by sensors. For this example a MakerLine sensor by Cytron is needed.
Uncomment the row <kbd>#define LIPO</kbd> if you're using ARLOK powered from a LiPo Battery so you can read the battery voltage on the display. You can attach the positive lead of the battery to A2 pin for reading voltage, this pin is defined by <kbd>#define LIPO_PIN</kbd>.

### Motors Setup

See [motors setup procedure](../motors_setup.md)

### Line sensors

In this example ARLOK use a sensor board called [Maker Line](https://docs.google.com/document/d/1wZwWl72CKkajTDIyiMxSQ3bwXbWbqW0eq7rdg2MUPeU/edit?usp=sharing), that simplify the Robot software and build. This board can be set to work with a light or dark line, with a button you can calibrate the 5 sensors and you have the possibility to use 5 digital output or only one analog output to check the sensors status.  

### Sensor calibration
For the calibration there is a switch on the left and a button on the right of the board. The switch is used for selecting the line color (Black line on a bright background or White line on a dark background). After you've selected the line color with the switch, you must power the board and keep the button on the right until 5 leds will light up all in sequence: after this led will flash and you must pass slowly the sensor across the line, then press the button again.  

[This video](https://drive.google.com/file/d/19okwq5Kp5xKjQq40woOOhy_JcsLVJZ87/view) shows how perform the line sensor calibration.

### Sensor usage
On ARLOK we'll use the analog output, connected to the Arduino A2 pin. The following table shows an example of the output voltage, depending on the position of the line with respect to the sensors.

| Line not found | Left ← → Center ← → Right | All sensors on |
| :---: | :---: | :---: |
| 0 - 0.5V | 0.5V ← → 2.5V ← → 4.5V | 4.5 - 5V |

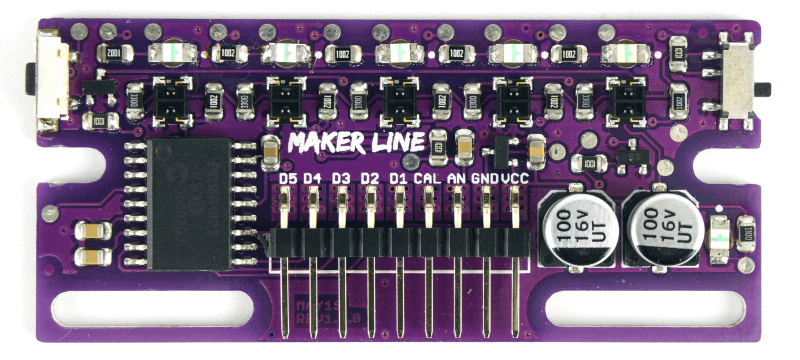
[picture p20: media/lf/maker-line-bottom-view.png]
MakerLine


In the upper side this board have 5 leds, that show which sensor is seeing the line. This feature is great for "interpreting" the Robot's behavior, and debugging your code.

### Mounting the board

ARLOK is designed for mounting the Maker Line sensor card, in the lower part there are two slotted holes, which allow you to mount the card in the desired position. You can use spacers given with the Makerline kit. In this code example is used the A2 Arduino pin, you also need to connect the GND pin and 5V pin, between the ARLOK shield and the Maker Line. To do this, there is a specific connector on the Arlok shield.

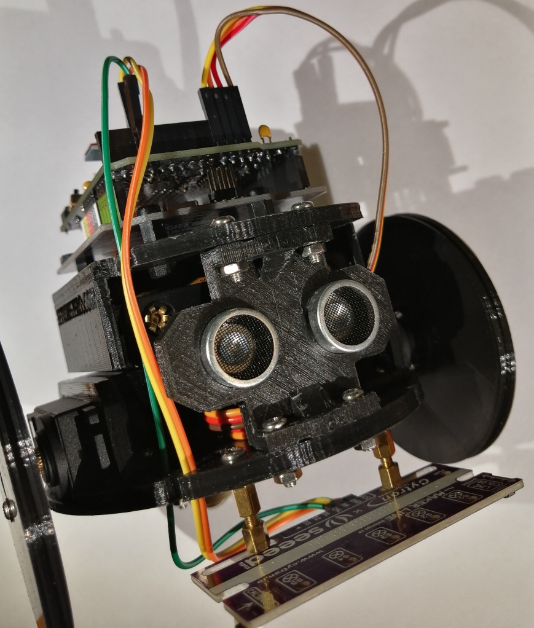
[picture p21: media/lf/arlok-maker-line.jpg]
ARLOK with Maker Line


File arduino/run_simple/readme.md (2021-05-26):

## Simple RUN

Arlok moves forward, when he see an obstacle will make a sound, stop, move back, then turn and continue.  

> For using the sketch with AR.L.O. PCB, comment the `#define ARLOK`

### Setup

There is a video showing this procedure but, sorry, the language used is italian: [https://youtu.be/qzJxrcuSvpU](https://youtu.be/qzJxrcuSvpU)

Press <kbd>P1</kbd>, keep it pressed and then turn on the power switch, release <kbd>P1</kbd> only when you see something appear on the display.  
When you see `ARLOK SET` you can power the motors too pressing the button on the rear.

First page of setup menù will allow you to set the _zero_ point for the left motor: turn the trimmer until motor stops, then press <kbd>P1</kbd> for saving: value will be saved into the eeprom and will be showed between parenthesis near `LEFT MOTOR` writing on the first row of the display.  
Now press <kbd>P2</kbd> for going to the second page of the setup menù.  

> If you know the value showed in parenthesis is already good (example: you're entered in the setup menù only for balancing), you can directly skip this page by pressing <kbd>P2</kbd> even the motor is running (because the motor in this moment is taking the value given by the trimmer, not the one saved into the eeprom).  

Second page will allow you to do the same for the right motor. So, follow the same steps you read for the left motor.  

Third page will give you the possibility for _balancing_ motors speed. You can notice ARLOK will not move in a straight line when moves forward: this because motors have some little differencies and there are no encoders and a _PID_ system for balancing them, so this simple method has been implemented (thx @MrLoba81) for compensating a little the two motors.  

Turning trimmer to the right will give more speed to the right motor, so if ARLOK tends to go to the right when moves forward, turning trimmer to the right will give more speed to the right motor and then compensate this behaviour. If ARLOK tends to go to the left when moves forward, you must turn the trimmer to the left. Values are experimental so it's possibile you must repeat this setup procedure more than one time.

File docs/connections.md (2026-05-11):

## Connections

In the following table are showed Arduino Uno/MakerUNO to Arlok shield connections.  

> Pinout is reported also for the older version named AR.L.O.  

If a cell is empty, means that pin is free to use and reported on a dedicate header. The `interrupt` column shows the interrupt number associated with the pin (valid only for boards with the ATmega328), but is reccomended to use the Arduino function `digitalPinToInterrupt(Pin)` such as used in the Arlok sketches.

| Arduino PIN | AR.L.O. (obsolete) | Arlok (current) | Notes | Interrupt |
|:--- |:--- |:--- |:--- |:--- |
| (empty) | | Not available | The unused pin near IOref | |
| IORef | | Not available | | |
| Reset | Reset Button | Reset Button | | |
| 3.3V | | | | |
| 5V | | | | |
| GND | | | | |
| GND | | | | |
| Vin | | Not available | unused on MakerUNO | |
| A0 | Trimmer VR1 | Trimmer VR1 | | |
| A1 | | | | |
| A2 | | | | |
| A3 | | | | |
| A4 | Don't use if OLED! | Not available | Shared with SDA | |
| A5 | Don't use if OLED! | Not available | Shared with SCL | |
| D0/RX | UART RX > COMM RX  | UART RX > COMM RX | | |
| D1/TX | UART TX > COMM TX  | UART TX > COMM TX | Through voltage divider | |
| D2 | Sonar - Echo | Pushbutton 1 | 'button' on MakerUNO | 0 |
| D3 | | Sonar - Echo | | 1 |
| D4 | | Sonar - Trigger | | |
| D5 | | Pushbutton 2 | | |
| D6 | Pushbutton 1 | | | |
| D7 | Pushbutton 2 | | | |
| D8 | Sonar - Trigger | Buzzer (if makerUNO is used)  | 'buzzer' on MakerUNO | |
| D9 | ServoMotor - Right | ServoMotor - Right | | |
| D10 | ServoMotor - Left  | ServoMotor - Left | | |
| D11 | | | | |
| D12 | | | | |
| D13 | | | | |
| GND | | | | |
| ARef | | | | |
| SDA | OLED SDA | OLED SDA + Grove + I2C header | Shared with A4 | |
| SCL | OLED SCL | OLED SCL + Grove + I2C header | Shared with A5 | |

### Connections considerations

- On Arlok shield some pin are not reported on the PCB (such as the `IOref` and the unused pin near it, `A4` and `A5`), so you can use fewer male headers.
- On both Arlok and AR.L.O., `A3` is used in some sketches as seed for random number generator initialization; so, if you want to use `A3` in your own application, please change the code accordly.
- On Arlok all free digital pins are reported on `EXT` header along with 5V and ground, and the 3 free analog inputs are reported on 3 separate headers having power supply each while on on AR.L.O. free digital pins are reported on 2 headers: `EXT2` (`D11`, `D12`, `D13`) and `EXT1` (`D3`, `D4`, `D5`) and the analog inputs are reported to simple pads.

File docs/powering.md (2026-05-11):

## Powering Arlok V1

You can power Arlok with 3 different methods:

- Using 7 AA Batteries: 4 for motors, 3 for logics (safe, adviced for kids, limited autonomy)
- Using 4 AA Batteries fot both motors and logics (cheap, not adviced, limited autonomy)
- Using a single 18650 LiPo Battery with step-up converter (rechargeable, dangerous, not adviced for kids, great autonomy)

### Using 7 AA Batteries (6V+4.5V)

This is a safe method since common batteries are used. Anyway the 4AA batteries have a limited autonomy since are used for motors and hare pretty difficult to replace since you must unscrew the top plate.
You need:

- 7 AA Batteries (not adviced NiMh rechargeable ones since are 1.2V)
- a battery holder for 4 AA batteries
- a battery holder for 3 AA batteries

6V+4.5V powering

The 3xAA Battery holder (4.5V) will be connected to the VDD screw terminal and will take place under the robot, near the ballcaster  
The 4xAA Battery holder (6V) will be connected to the VSERVO screw terminal through the pushbutton. This holder will take place between the top and the bottom plate  
You must put the JP1 jumper in the VDD position

### Using 4 AA Batteries (6V)

This method is cheap but not adviced.
You need:

- 4 AA Batteries (not adviced NiMh rechargeable ones since are 1.2V)
- a battery holder for 4 AA batteries

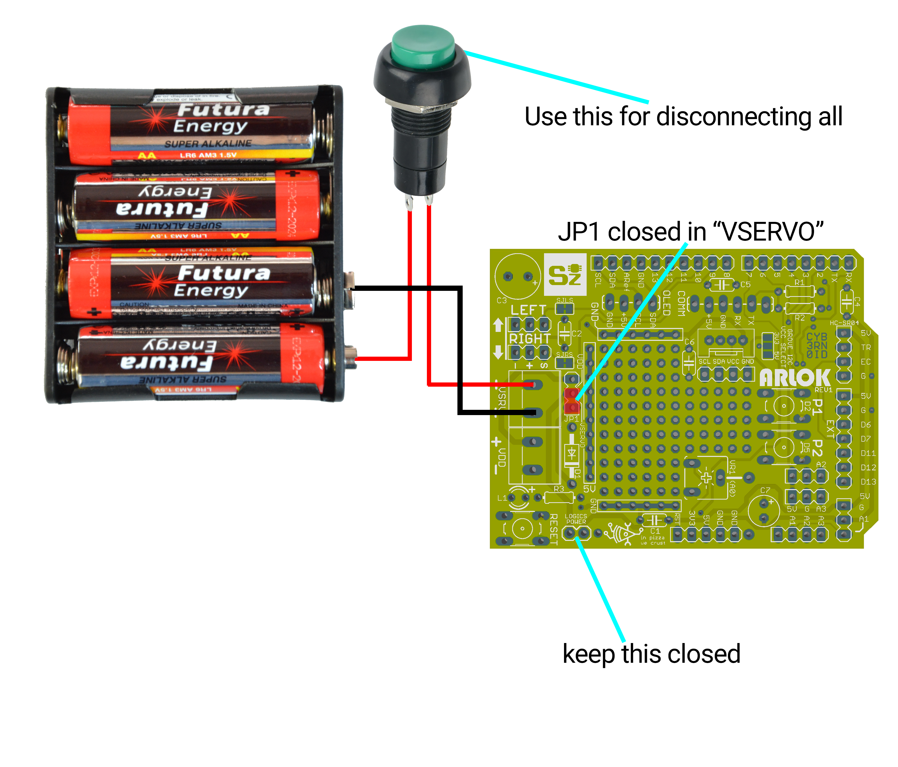
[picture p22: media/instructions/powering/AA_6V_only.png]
6V powering
  

The 4xAA Battery holder (6V) will be connected to the VSERVO screw terminal through the pushbutton. This holder will take place between the top and the bottom plate.  
You must put the JP1 jumper in the VSERVO position and you can close the the "logics" pad

### Using a 18650 LiPo cell

See the [lipo_mod.md document](lipo_mod.md)

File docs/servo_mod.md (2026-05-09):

## Servo hack

This is a simple guide for hacking a standard **analog** servo for achieving continuous rotation. This procedudre is **not needed** if you have 360° servo.
[Here is a video](https://www.youtube.com/watch?v=_Ubauj75d9E) Showing this procedure

> Note: a **digital** servo cannot be used to do this mod since it has a microcontroller inside that will stop the motor when he detects the servo cannot reach the desired position

Tools needed:

- 4 2.2K ¼W 1% resistors
- a lancet (for plastic gears servo) or a small wrench (for metallic gears servo)
- a small phillips screwdriver
- soldering iron
- solder sucker

Locate the 4 screw in the lower part of the servo:  

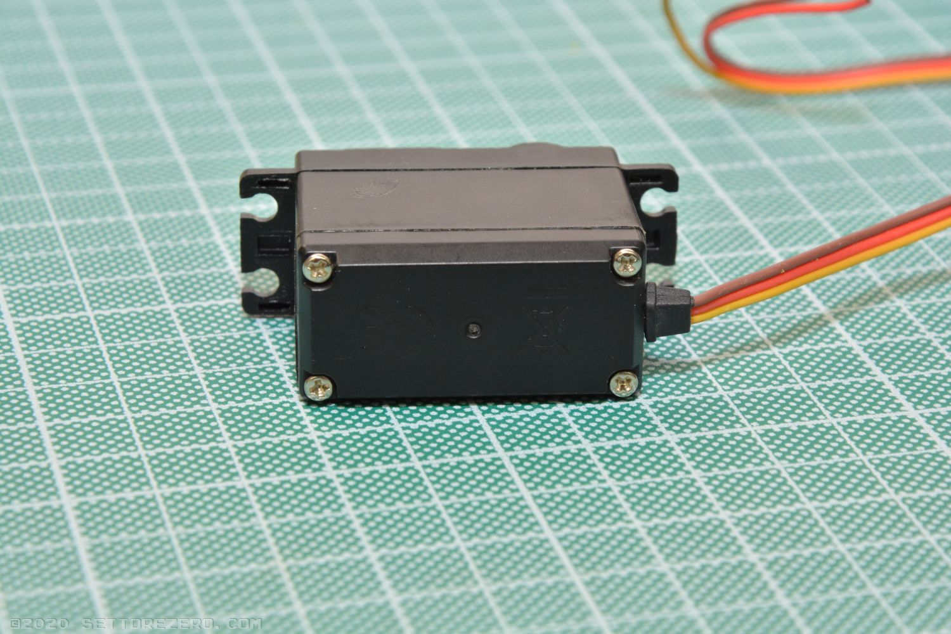
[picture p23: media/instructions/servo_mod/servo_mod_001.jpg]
servo mod


Unscrew the screws:

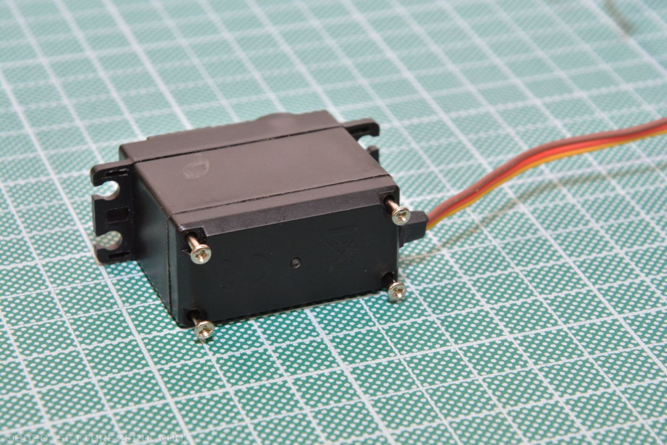
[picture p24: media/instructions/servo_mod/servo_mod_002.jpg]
servo mod


Disassemble the servo box:

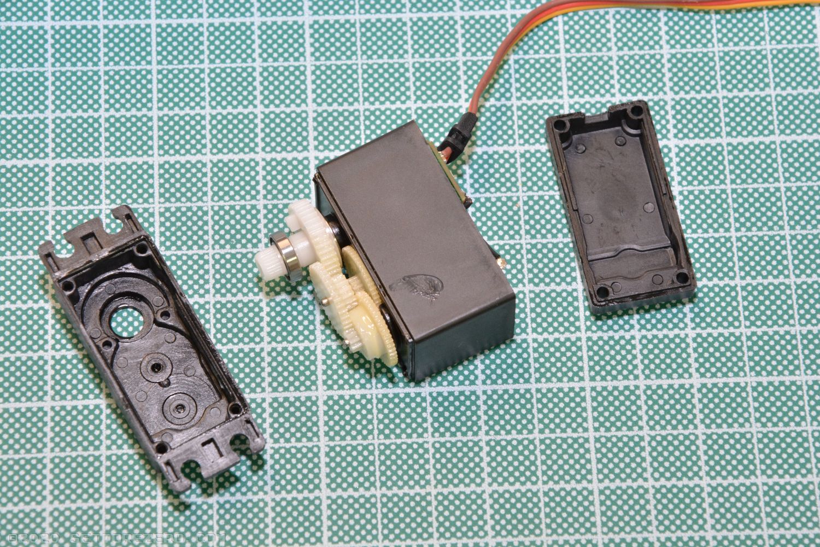
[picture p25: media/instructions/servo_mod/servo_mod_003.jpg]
servo mod


Locate the gears:

servo mod

Extract the gear with the hub and the ball-bearing on it:

servo mod

Look at this gear: it has a small notch under the ball-bearing. The MG996R servo has a little metallic cilinder instead:

servo mod

Now you must remove this notch. For a servo having plastic gears you can gently use a lancet or a small cutter: don't apply too much force OR THE ENTIRE GEAR WILL BROKE! For the MG996R servo you can use a small wrench for extracting the metallic notch by simply pulling it upward:

servo mod

Now extract the servo PCB:

servo mod

In the top part of the servo there is the potentiometer hub: is the one where the gear you've previously removed was placed. Gently press the potentiometer hub backward for pushing it out:

servo mod

Now you've the potentiomer and pcb out:

servo mod

Desolder the cables from the potentiomer:

servo mod

Arrange the 2 2.2KΩ 1% resistor in this way:

servo mod

Put the resistors in place of the potentiomer:

servo mod

Re-assemble the servo. Do the same to other servo.

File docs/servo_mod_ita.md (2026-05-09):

## Modifica servocomandi

Questa è una guida per eseguire la modifica di un normale servocomando RC **analogico** in modo da trasformarlo in un servo a rotazione continua. Questa procedura **non è necessaria** se hai già un servo a 360°.  
[Qui c'è un video](https://www.youtube.com/watch?v=_Ubauj75d9E) che illustra questa procedura.

> Nota: un servocomando **digitale** purtroppo non puó essere utilizzato per la modifica in quanto all'interno ha un microcontrollore che ferma il motore se rileva che il motore non arriva mai in posizione.

Materiale necessario:

- 4 resistenze 2.2KΩ ¼W 1%
- un piccolo bisturi/taglierino (se hai un servo con ingranaggi di plastica) o una pinza (se hai un servo con ingranaggi metallici)
- un piccolo cacciavite a croce
- saldatore
- aspirastagno

gira il servocomando dalla parte delle 4 viti di chiusura nella parte bassa:

servo mod

Svita le viti:

servo mod

Apri la scatola del servocomando:

servo mod

Visualizza gli ingranaggi:

servo mod

Estrai l'ingranaggio del mozzo e il cuscinetto a sfera su di esso:

servo mod

Guarda questo ingraggio: ha un nottolino al di sopra, nei servo con ingranaggi metallici, come il MG996R, è metallico:

servo mod

Quel nottolino serve a bloccare la rotazione continua dell'ingranaggio: bisogna rimuoverlo. Nei servo in plastica puoi tagliarlo con il bisturi (ma questa procedura non è reversibile!): fai con estrema cura senza applicare troppa forza altrimenti rischi di rompere l'ingranaggio!
Nei servo metallici il nottolino può essere estratto con una pinza dato che, generalmente, viene inserito a pressione in un foro:

servo mod

Estrai il circuito stampato del servocomando:

servo mod

Nella parte superiore del servocomando spunta fuori l'alberino del potenziometro: devi premerlo con delicatezza verso il basso per far fuoriuscire il potenziometro:

servo mod

Devi avere PCB e potenziometro a portata di mano:

servo mod

Dissalda i cavetti (o i terminali) del potenziometro:

servo mod

Prendi le resistenze da 2.2KΩ 1% e arrangiale in questo modo:

servo mod

Metti le resistenze nei pad che erano riservati al potenziometro. In questo modo il controller del potenziometro crederà che il servo si trova sempre in posizione centrale per cui non smetterà mai di far girare il motore (a meno che non gli inviamo il segnale di posizione centrale):

servo mod

Rimonta il servo. Fai lo stesso con l'altro servo.

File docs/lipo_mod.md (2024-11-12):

## MOD : Using LiPo Batteries

Warning: LiPo batteries can be very dangerous! Handle them with care and make this mod at your own risk!

### Preliminary stuff
  
#### You'll need:
- 18650 LiPo Battery with tabs
- an SX1308 Step-Up Converter (PCB signature is HW668)
- a TP4056 with protection for recharging the battery (or use the method you prefer for re-charge the battery)
- 3D-print the [`arlok_18650_holder.stl`](../cad/stl/arlok_18650_holder.stl)
- additional 2 M3 screws, Allen bolt socket cap, 12mm (length of threaded part - 15mm total) + nuts
- some strong double-sided tape 

OPTIONAL 
- Display having leds in shape of a battery ("Battery display"), indicating charge level of 1S Lipo Battery (PCB signature is XW228DKFR4)
- Alternate "Plate Top" STL [`arlok_plate_top_1sdisplay.stl`](../cad/stl/arlok_plate_top_1sdisplay.stl) having a slot for the TP4056 with protection and the square hole for the above mentioned display 

Boards

#### You'll remove:
- Battery Holder for 4AA batteries
- Battery Holder for 3AA batteries
- X2 (VDD) Screw Terminal 2pin

#### You'll not use anymore:
- Power Jumper (you can close it with a bridge)

#### Schematic (basic)

18650 powering

#### Schematic (with 1S battery display)

18650 powering + display

### How-to 

- Fix the 18650 battery on the bottom of the robot using the `arlok_18650_holder.stl`, screws and bolts
- Solder a red cable from the + tab of the battery to 1 pin of the round pushbutton with retain or lever switch
- Solder a red cable from the free button/switch terminal to the + Input terminal of the SX1308 module
- Solder a black cable from the - tab of the battery to the - Input terminal of the SX1308 module 
- Turn on the button/switch and check with a multimeter the SX1308 module: adjust it using the multi-turn trimmer on it for 5.6 / 5.7 volts (the Diode D1 will lower the voltage of about 0.6-0.7V)
- Turn off the button 
- Attach the SX1308 module on the top of a servo bracket using double-sided tape (or make and share your own design)
- Solder a red cable from the SX1308 + output to the + of Vservo X1 screw terminal 
- Solder a black cable from the SX1308 - output to the - of Vservo X1 screw terminal 
- (optional) Solder a cable, having a female dupont terminal, on the + Input terminal of the SX1308 module along with red cable already soldered: this can be used for checking the battery voltage reading from an Analog Input. The female dupont terminal can be connected to one free analog input terminal (A2 - you can use/take inspiration from the [explorer lipo](../arduino/explorer_lipo/) programming example)
- Set the Jumper JP1 in the `VSERVO` position

OPTIONAL 
- Solder red and black cables on the "Battery Display" and connect them to VIN and GND of the SX1308 PCB

Now all the robot parts (logics and servos) will be powered from the same battery: Logics will be powered at about 5V and servo at about 5.6V.  
The [explorer](../arduino/explorer/) program contain some instructions for reading the battery and show it on display.

For charging the battery you must:
- Turn off the button/switch on the back
- Attach outputs of the TP4056 module on the battery using alligator clips (or make and share your own design)
- Battery will be fully charged when blue led on TP4056 module turns on

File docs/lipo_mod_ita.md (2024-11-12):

## MOD : Utilizzo batterie LiPo

Attenzione: Le Batterie LiPo possono essere molto pericolose se non vengono maneggiate e gestite correttamente! Fate questa modifica a vostro rischio!

### Operazioni preliminari
  
#### Avrai bisogno di:
- Una batteria LiPo formato 18650 munita di linguette a saldare, più alta è la capacità, più tempo funzionerà il robot
- Un [convertitore Step-Up SX1308](https://amzn.to/3L3Qqu7)
- Un caricabatterie per singola cella LiPo [TP4056 munito di protezione](https://amzn.to/3ZIwKjv) (oppure utilizza il metodo che preferisci per ricaricare la batteria)
- Stampa in 3D del pezzo [`arlok_18650_holder.stl`](../cad/stl/arlok_18650_holder.stl)
- Due viti M3, lunghezza parte filettata 12mm, + 2 dadi
- Nastro biadesivo
- Cavetti nero e rosso

OPZIONALE 
- Display con led disposti a forma di batteria ([Battery Display 1S](https://amzn.to/4ermYJs)) che indica il livello di carica di una cella Litio 1S 
- Pezzo alternativo del Plate Top [`arlok_plate_top_1sdisplay.stl`](../cad/stl/arlok_plate_top_1sdisplay.stl) che contiene sia l'incavo per incastrare il TP4056 sia la finestra laterale per incastrare il Battery Display

Boards

#### Dovrai rimuovere/dissaldare:
- Il portabatterie 4xAA
- Il portabatterie 3xAA
- I cavi dall'interruttore sul pilastrino posteriore
- (optional per non confondersi) Lo screw terminal X2 (VDD)

#### Non userai più
- L'interruttore/Il jumper "Power" (i pad devono essere chiusi permanentemente, userai il tasto sul retro per accendere tutto. Se hai utilizzato un jumper, puoi lasciare questo sempre chiuso)

#### Schema (senza display)

18650 powering

#### Schema (con display)

18650 powering+display

### Procedimento

- Fissa la batteria 18650 sul fondo del robot utilizzando il pezzo [`arlok_18650_holder.stl`](../cad/stl/arlok_18650_holder.stl), le viti e i dadi
- Salda un cavetto rosso dalla linguetta + della batteria ad uno dei due pin dell'interruttore sul pilastrino posteriore
- Salda un cavetto rosso dall'altro pin dell'interruttore all'ingresso + del modulo Step-Up SX1308
- Salda un cavetto nero dalla linguetta - della batteria all'ingresso - del modulo Step-Up SX1308
- Premi l'interruttore (accendi) e con un multimetro verifica l'uscita del modulo SX1308: regola il trimmer multigiro per avere in uscita circa 5.6 / 5.7 volts (il Diodo D1 provvederà ad una caduta di tensione di 0.6-0.7V). Per sicurezza puoi controllare la tensione sul catodo del diodo D1 per essere sicuri che ci siano 5V
- Premi di nuovo l'interruttore per spegnere
- Fissa il modulo SX1308 su uno dei due supporti dei servo utilizzando il nastro biadesivo (oppure crea tu, e condividi, la tua soluzione)
- Salda un cavetto rosso dall'uscita + del modulo SX1308 al terminale + del connettore a vite X1 (VSERVO) sul PCB
- Salda un cavetto nero dall'uscita - del modulo SX1308 al terminale - del connettore a vite X1 (VSERVO) sul PCB
- (opzionale) Salda un cavetto del colore che vuoi (ma non nero, nè rosso per non creare confusione), munito di connettore dupont femmina ad una estremità, all'ingresso + del modulo SX1308 insieme al cavetto che già hai saldato: questo cavetto sarà utilizzato per controllare la tensione della batteria tramite un ingresso Analogico. Il connettore dupont femmina andrà collegato ad un ingresso analogico libero (ad esempio A2 come illustrato nell'esempio [explorer lipo](../arduino/explorer_lipo/))
- Imposta il jumper JP1 nella posizione `VSERVO`

Da questo momento tutto il robot (sia la parte logica che i servocomandi) saranno alimentati dalla stessa batteria: la logica avrà una tensione di circa 5V (uscita SX1308 scalata dal diodo D1) mentre i servocomandi saranno alimentati a circa 5.6V.
L'esempio [explorer](../arduino/explorer/) contiene il codice per leggere la tensione della batteria LiPo e mostrarla sul display.

Per caricare la batteria bisognerà:  

- Spegnere il robot agendo sull'interruttore
- Collegare le uscite del modulo TP4056 sulla batteria 18650 utilizzando, magari delle clips coccodrillo (oppure crea tu, e condividi, la tua soluzione)
- La batteria è completamente carica quando si accende il led blu sul modulo TP4056

### Avvertenze:

- non caricare mai la batteria con l'interruttore acceso: ovvero non alimentare il robot e contemporaneamente caricare la batteria
- mentre carichi il robot, questo dovrebbe essere messo in un luogo sicuro, lontano da oggetti infiammabili o suscettibili di esplosione. Preferibilmente tieni in carica il robot in un contenitore a prova di esplosione
- esegui collegamenti puliti, utilizza il termorestringente per coprire le zone di alimentazione scoperte: un cortocircuito su una batteria LiPo è molto pericoloso
- tenere lontano dalla portata dei bambini


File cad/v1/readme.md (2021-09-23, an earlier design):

# Arlok CAD Files

- [STL](./stl) folder contains file to be 3D-printed
- [STEP](./step) folder contains step files if you want to import them in a 3D-modeling software

> Quick link to this page: [https://tinyurl.com/3dprintarlok](https://tinyurl.com/3dprintarlok)

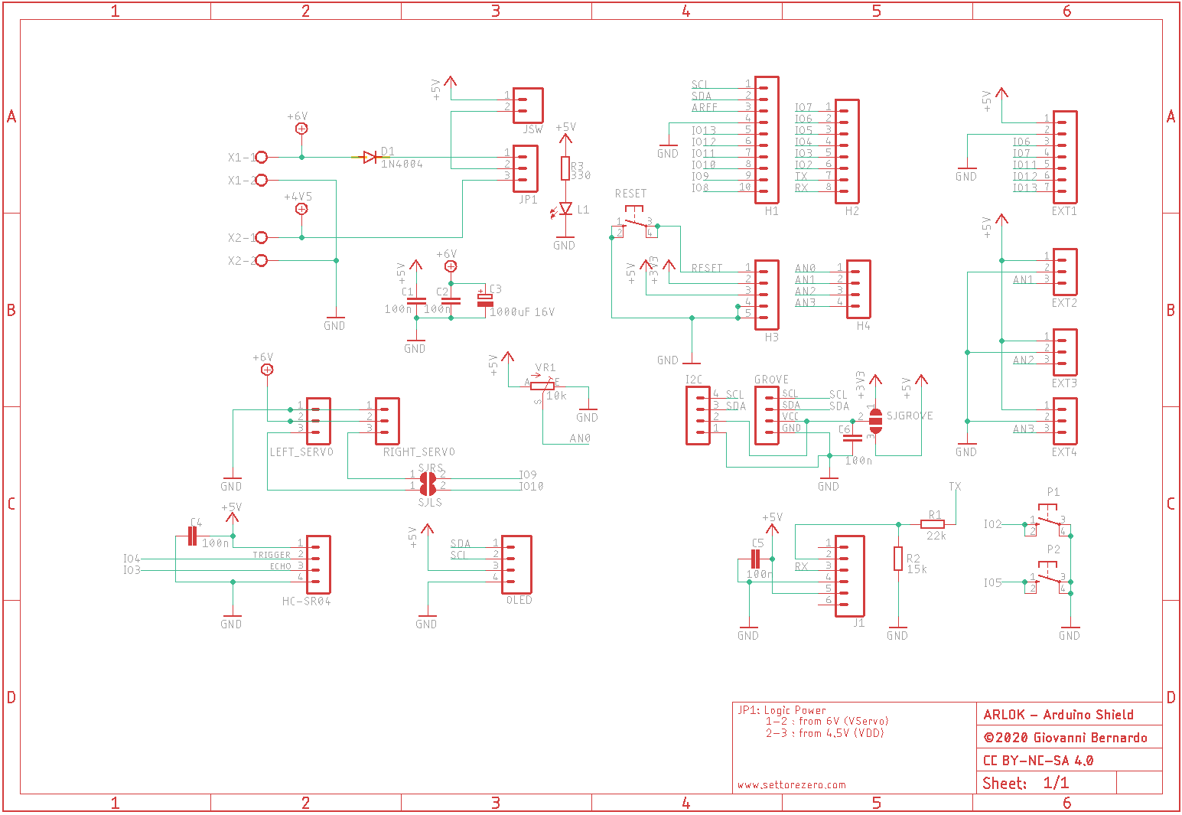
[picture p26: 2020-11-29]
docs/arlok_schematic_oldrev.png

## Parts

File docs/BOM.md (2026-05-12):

## ARLOK Bill Of Materials

> Quick link to this page: [https://tinyurl.com/shieldarlok](https://tinyurl.com/shieldarlok)  

### Summary

1) [Electronics - PCB](#pcb)
2) [Electronics - Shield Components, detailed list](#shield)
3) [Electronics - Shield Components, shopping list](#shieldc)
4) [Electronics - External components](#ext)
5) [Mechanics   - 3D-printed parts](#3d)
6) [Mechanics   - Components](#mech)
7) [Adviced Arduino UNO R3 compatible Boards](#boards)
8) [Differencies between REV1 and first rev PCB](#diffrev1)

### 1) Electronics - PCB

Step 1: Subscribe to PCBWay using my invite link:
        https://www.tinyurl.com/pcbwaysz

Step 2: Order the ARLOK shield REV1 PCB from the following link:
        [https://tinyurl.com/arlokshieldr1](https://tinyurl.com/arlokshieldr1)

> If you don't want to buy the PCB you can consider to use one of that [protoshields](https://amzn.to/4d3CUo2) keeping in mind the [schematic](./arlok_schematic_rev1.png) and/or the [connection table](./connections.md)  
Maybe the following simplified schematic can be useful too:

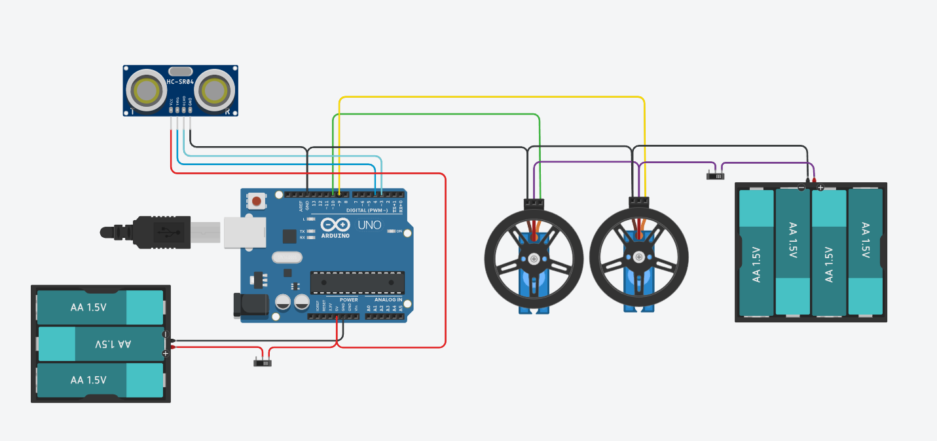
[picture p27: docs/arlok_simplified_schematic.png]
Arlok Simplified Schematic


Please note: Arlok V2 will not use AA Batteries

### 2) Electronics - Shield REV1 Components (detailed)

> You can download the following [list in PDF format](./pdfs/arlok_shield_BOM.pdf)

| Part | Value | Notes |
| --- | --- | --- |
| C1 | 100nF multilayer | 5mm pitch |
| C2 | 100nF multilayer | 5mm pitch |
| C3 | 1000uF 16V electrolytic | 3.5mm pitch - 8mm dia. |
| C4 | 100nF multilayer | 5mm pitch |
| C5 | 100nF multilayer | 5mm pitch |
| C6 | 100nF multilayer | 5mm pitch |
| C7 | 220uF 16V electrolytic | 2.5mm pitch - 6mm dia. |
| D1 | 1N4007 | good any 1N400x |
| R1 | 22KΩ ¼W | red - red - orange |
| R2 | 15KΩ ¼W | brown - green - orange |
| R3 | 330Ω ¼W | orange - orange - brown |
| P1 | tactile switch | 6x6mm (adviced long button) |
| P2 | tactile switch | 6x6mm (adviced long button) |
| RESET | tactile switch | 6x6mm |
| VR1 | 5kΩ ÷ 20kΩ trimmer | 6x6mm |
| L1 | led 3mm | |
| H1 (*) | male pinheader 10pin | Arduino header - solder on top |
| H2 (*) | male pinheader 8pin | Arduino header - solder on top |
| H3 (*) | male pinheader 5pin | Arduino header - solder on top |
| H4 (*) | male pinheader 4pin | Arduino header - solder on top |
| EXT (EXT1)  | male pinheader 7pin | |
| EXT2 (A1) | male pinheader 3pin | |
| EXT3 (A2) | male pinheader 3pin | |
| EXT4 (A3) | male pinheader 3pin | |
| HC-SR04 | male pinheader 4pin | |
| I2C | male pinheader 4pin | optional |
| J1 (COMM) | female pinheader 6pin | |
| JP1 | male pinheader 3pin + jumper | |
| JSW (POWER) | male pinheader 2pin + jumper | or 2.54mm pitch lever switch |
| LEFT_SERVO  | male pinheader 3pin | |
| RIGHT_SERVO | male pinheader 3pin | |
| OLED | female pinheader 4pin | |
| X1 | Screw Terminal 2pin | 5mm pitch |
| X2 | Screw Terminal 2pin | 5mm pitch |
| GROVE | GROVE male header | optional |

> (*) Standard headers are 11mm long: those are good if you use one of the Adviced Boards (see below). If you want to use a standard Arduino UNO, 11mm headers are not good, since the USB connector will touch under Arlok shield, so in this case 15mm headers are needed or you can use special Arduino Headers

> Note: if you must mod the servos for the continuous rotation, you need further 4 2.2KΩ ¼W resistors, adviced at 1% tolerance

### 3) Electronics - Shield REV1 Components (shopping list)

| Qt. | Part |
| --- | --- |
| 5 | 100nF multilayer capacitor,  pitch 5mm |
| 1 | 1000uF 16V electrolytic capacitor, pitch 3.5mm dia 8mm |
| 1 | 220uF 16V electrolytic capacitor, pitch 2.5mm dia 6mm  |
| 1 | 1N400x diode |
| 1*  | 22KΩ ¼W 1% resistor |
| 1 | 15KΩ ¼W resistor |
| 1 | 330Ω ¼W resistor |
| 2 | tactile switch 6x6mm, long button |
| 1 | tactile switch 6x6mm |
| 1 | 5kΩ ÷ 20kΩ trimmer (6x6mm) |
| 1 | LED 3mm |
| 2 | Screw terminal, pitch 5mm |
| 2 | 40pin male headers (needed 60pin) |
| 1 | female header (needed 6+4 pin) |
| 1 | jumper block, pitch 2.54mm |
| 1 | PCB lever switch, pitch 2.54mm (**) |

> (*) If you must mod the servos for the continuous rotation, you need further 4 22KΩ ¼W resistors, adviced at 1% tolerance
> (**) Or 2 pin-male header + jumper block
> The Arduino Shield is good for both V1 and V2 Arlok variants

### 4) Electronics - External components

| Qt. | Description |
| --- | --- |
| 1x  | Adviced Arduino UNO compatible board (*) |
| 2x  | Servo MG996R (or other analog servo) modded for continuos rotation OR Servo having 360° rotation |
| 1x  | HC-SR04 Ultrasonic sensor |
| 1x  | Bluetooth module HC-05 (or HC-06) - Needed for Bluetooth remote example |
| 1x  | Cytron MakerLine board - Needed for Line Follower example |
| 1x  | OLED display module I2C (4pin) 0.96" |
| 1x  | Battery Holder for 4AA batteries |
| 1x  | Battery Holder for 3AA batteries |
| 1x  | Round pushbutton with retain or lever switch or round rocker switch (**) |
| 1x  | 4pin Female/Female Dupont cable (~15cm) (***) |
| 7x  | AA 1.5V Batteries (****)  NOT for Arlok V2 |

(*) See list below

(**)  Print the `arlok_pillar_hole_xx.stl` according the pushbutton diameter  

(***) Used for connecting ultrasonic module to PCB, you can use also 4 separate F/F jumper
     cables or make your own cable using connector you prefer.

(****) Not adviced to use NiCd or NiMH batteries, since voltage of those batteries is 1.2V. There is also a mod for using one LiPo Battery but it's at your own risk
     read more here: [LiPo Mod](lipo_mod.md). If you printed the Arlok V2 variant, you cannot use AA batteries since there is no room for them: Arlok V2 uses a single 18650

### 5) Mechanics - 3D-printed parts

Please see in the [cad folder](../cad)

### 6) Mechanics (Only for v1 files) - Components

Please note: following hardware parts are only used for v1 3d printed files. The V2 will use different components

| Qt. | Description |
| --- | --- |
| 12x | M3 screw, Allen bolt socket cap, 12mm (length of threaded part - 15mm total) |
| 8x  | M3 screw, Allen bolt socket cap, 6mm (length of threaded part - 8mm total) |
| 14x | M3 washers (optional) |
| 12x | M3 nuts |
| 2x  | M3 screw, Countersunk, 8mm (length of threaded part, 10mm total) |
| 4x  | Hex spacer Female/Female 8 or 10mm length |
| 1x  | Tamiya BallCaster model 70144 (*) |
| 2x  | Rubber O-Ring, 70mm internal diameter, 2-3mm width (**) |

[Here is a picture showing screws](../media/arlok_screws.jpg). Same picture is available [in italian too](../media/arlok_screws_ita.jpg).

(*) when you buy the Tamiya 70144 ballcaster kit, there are parts for making 2 ballcasters. Maybe you can share the extra ballcaster part with a friend so he can build an Arlok too. Alternatively you can 3D-print the [Ball Caster V2 on Thingiverse](https://www.thingiverse.com/thing:1408935) in the height of 30mm (you need [OpenScad](https://openscad.org/) for editing the .scad file and change the height)

(**) There are some kinds of tires that can be 3D-Printed using TPU. If your 3D printer can handle TPU, try first to print them yourself: see in [STL folder](../cad/v1/stl) for the Tires.

### 7) Adviced Arduino UNO R3 compatible boards

Since the Arlok shield is designed using an Arduino UNO shape as reference, microcontroller boards having "tall" parts (the USB type B connector, like on the original Arduino UNO R3), cannot be used since USB connector metallic part can touch the solder side of the shield causing short circuits and then damages.  
Only way to use a genuine Arduino UNO R3 board is to assemble the shield using not-so-common long male headers (15mm at least).  
Here is a list of suitable boards don't using the USB type B connector:  

- [Keyestudio 328 Plus](https://www.keyestudio.com/products/2020-new-keyestudio-plus-development-board-with-type-c-interface-usb-cable-compatible-with-arduino-uno-r3)
- [Cytron Maker UNO](https://www.cytron.io/p-maker-uno-simplifying-arduino-for-education)
- [Arduino Make Your UNO](https://store.arduino.cc/pages/make-your-uno-kit) 
- [Seeeduino 4.2](https://www.seeedstudio.com/Seeeduino-V4-2-p-2517.html)
- [Grove Beginner Kit](https://www.seeedstudio.com/Grove-Beginner-Kit-for-Arduino-p-4549.html)

Some of those boards have a full-size barrel jack connector: this can touch the shield so is adviced to desolder it 

### 8) Differencies between REV1 and first rev PCB

- Added C7 for having a little more energy buffer for devices
- Added a via (not connected) next GND of the power header if you want to connect to the Arduino VIN pin 
- Changed silkscreen of the JSW connector from "POWER" to "LOGICS POWER" since is used only for 5V
- Added a via (not connected) next to the JSW connector if you want to use a three pins switch
- Changed VR1 from PT10LV10 (10x10mm) type to a smallest and more common 6x6mm (there is an additional via for the center pin for using a 10x10mm anyway)
- Added "A0" next VR1 silkscreen to remember where trimmer is connected 
- Enlarged the prototyping area adding further 21 vias
- Changed silkscreen for the screw terminals connector: removed the minus sign allowing writings to be more readable
- Removed the OR logo and added the "Pizza Robotics - In pizza we crust" one

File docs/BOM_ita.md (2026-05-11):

## Elenco componenti ARLOK

> Link rapido a questa pagina: [https://tinyurl.com/bomarlokita](https://tinyurl.com/bomarlokita)  

Un elenco componenti con il link dove acquistarli è presente qui: [https://tinyurl.com/bomarlok](https://tinyurl.com/bomarlok)

### Indice

1) [Parte Elettronica - PCB](#pcb)
2) [Parte Elettronica - Componenti PCB rev.1, in dettaglio](#shield)
3) [Parte Elettronica - Componenti PCB rev.1, lista della spesa](#shieldc)
4) [Parte Elettronica - Componenti esterni](#ext)
5) [Parte Meccanica - Pezzi da stampare in 3D](#3d)
6) [Parte Meccanica - Altro](#mech)
7) [Schede compatibili Arduino UNO R3 consigliate](#boards)
8) [Differenze tra PCB REV1 e prima release](#diffrev1)

### 1) Parte Elettronica - PCB

Step 1: Iscriviti a PCBWay utilizzando il mio link di invito:
        https://www.tinyurl.com/pcbwaysz

Step 2: Ordina lo Shield di Arlok, revisione 1, utilizzando questo link:
        [https://tinyurl.com/arlokshieldr1](https://tinyurl.com/arlokshieldr1)

> Se non vuoi comprare il PCB di Arlok, potresti anche utilizzare un protoshield per Arduino UNO facendo tu i collegamenti seguendo lo [schema elettrico](arlok_schematic_rev1.png) e/o la [tabella delle connessioni](connections.md)  

### 2) Parte Elettronica - Componenti PCB rev.1, dettaglio

> Puoi anche scaricare questo elenco dal seguente link: [Elenco componenti in formato PDF](./pdfs/arlok_shield_BOM.pdf)  

| Componente  | Valore | Note |
| --- | --- | --- |
| C1 | 100nF multilayer | passo 5mm |
| C2 | 100nF multilayer | passo 5mm |
| C3 | 1000uF 16V electrolytic | passo 3.5mm - dia. 8mm |
| C4 | 100nF multilayer | passo 5mm |
| C5 | 100nF multilayer | passo 5mm |
| C6 | 100nF multilayer | passo 5mm |
| C7 | 220uF 16V elettrolitico | passo 2.5mm - dia. 6mm |
| D1 | 1N4007 | va bene un qualsiasi 1N400x |
| R1 | 22KΩ ¼W | rosso - rosso - arancio |
| R2 | 15KΩ ¼W | marrone - verde - arancio |
| R3 | 330Ω ¼W | arancio - arancio - marrone |
| P1 | pulsantino da pcb | 6x6mm (consigliato pulsante alto) |
| P2 | pulsantino da pcb | 6x6mm (consigliato pulsante alto) |
| RESET | pulsantino da pcb | 6x6mm |
| VR1 | trimmer 5kΩ ÷ 20kΩ | 6x6mm |
| L1 | led 3mm | |
| H1 (*) | pinheader maschio 10pin | Header Arduino - saldare da sopra |
| H2 (*) | pinheader maschio  8pin | Header Arduino - saldare da sopra |
| H3 (*) | pinheader maschio  5pin | Header Arduino - saldare da sopra |
| H4 (*) | pinheader maschio  4pin | Header Arduino - saldare da sopra |
| EXT (EXT1)  | pinheader maschio  7pin | |
| EXT2 (A1) | pinheader maschio  3pin | |
| EXT3 (A2) | pinheader maschio  3pin | |
| EXT4 (A3) | pinheader maschio  3pin | |
| HC-SR04 | pinheader maschio  4pin | |
| I2C | pinheader maschio  4pin | opzionale |
| J1 (COMM) | pinheader femmina  6pin | |
| JP1 | pinheader maschio  3pin + jumper | |
| JSW (POWER) | pinheader maschio  2pin + jumper | o interruttore a slitta passo 2.54mm |
| LEFT_SERVO  | pinheader maschio  3pin | |
| RIGHT_SERVO | pinheader maschio  3pin | |
| OLED | pinheader maschio  4pin | |
| X1 | Terminale a vite 2pin | 5mm pitch |
| X2 | Termninale a vite  2pin | 5mm pitch |
| GROVE | Connettore GROVE maschio da PCB  | opzionale |

> (*) Gli headers maschio standard sono lunghi 11mm : questi vanno bene soltanto se utilizzi una delle board Aduino UNO compatibili consigliate (vedi più in basso). Se vuoi utilizzare un Arduino UNO standard, gli headers da 11mm non vanno bene perchè il connettore USB tocca sulle saldature del PCB; in questo caso devi utilizzare degli header maschio da 15mm (più difficili da trovare) oppure gli header Arduino standard (passanti, femmina sopra e maschio sotto)  

> Nota: se devi eseguire la modifica dei servocomandi per la rotazione continua, sono necessarie altre 4 resistenze 22KΩ ¼W, possibilmente all'1% di tolleranza

### 3) Parte Elettronica - Componenti PCB rev.1, lista della spesa

| Qt. | Componente |
| --- | --- |
| 5 | Condensatore multilayer 100nF, passo 5mm |
| 1 | Condensatore elettrolitico 1000uF 16V, passo 3.5mm dia. 8mm |
| 1 | Condensatore elettrolitico 220uF 16V, passo 2.5mm dia. 6mm  |
| 1 | Diodo 1N400x |
| 1*  | Resistenza 22KΩ ¼W |
| 1 | Resistenza 15KΩ ¼W |
| 1 | Resistenza 330Ω ¼W |
| 2 | Pulsante da pcb 6x6mm, asta lunga |
| 1 | Pulsante da pcb 6x6mm |
| 1 | Trimmer 5kΩ ÷ 20kΩ  formato 6x6mm |
| 1 | LED 3mm |
| 2 | Terminale a vite da PCB, passo 5mm |
| 2 | Header maschio da 40pin (da dividere in pezzi) |
| 1 | Header femmina da 40pin (da tagliare in pezzi) |
| 1 | Blocchetto jumper passo 2.54mm |
| 1 | Interruttore a levetta da PCB, passo 2.54mm (**) |

> (*) se devi eseguire la modifica dei servocomandi per la rotazione continua, sono necessarie altre 4 resistenze 2.2KΩ ¼W, possibilmente all'1% di tolleranza  

> (**) oppure un blocchetto jumper, e utilizzi due pinheader maschio + il blocchetto jumper come se fosse un interruttore

### 4) Parte Elettronica - Componenti esterni

| Qt. | Descrizione |
| --- | --- |
| 1x  | Board Arduino UNO compatibile consigliata (*) |
| 2x  | Servocomando MG996R (o altro servo analogico) modificato a 360° o servo a rotazione continua |
| 1x  | Sensore Ultrasuoni HC-SR04 |
| 1x  | Modulo Bluetooth HC-05 (or HC-06) - Per esempio Bluetooth |
| 1x  | Modulo Cytron MakerLine - Per esempio Line Follower |
| 1x  | Display OLED 0.96" I2C |
| 1x  | Portabatterie per 4AA |
| 1x  | Portabatterie per 3AA |
| 1x  | Pulsante rotondo a ritenuta o interruttore a levetta (**) |
| 1x  | Cavo dupont femmina/femmina a 4 pin (~15cm) (***) |
| 7x  | Batteria AA 1.5V (****) |

(*) Vedi lista più in basso  

(**)  Ricordati di stampare in 3D il pezzo `arlok_pillar_hole_xx.stl` in base al diametro dell'interruttore che acquisti  

(***) Questo è usato per collegare il modulo ultrasuoni al PCB: puoi anche usare 4 cavetti jumper F/F, oppure rimuovi gli header e saldi dei fili... fa come preferisci  

(****) Non è consigliato utilizzare batterie NiCd o NiMH batteries dato che la tensione di queste batterie è 1.2V, quindi troppo bassa e può causare malfunzionamenti. In alternativa potresti seguire la guida per fare la [modifica con le batterie LiPo](lipo_mod_ita.md)  

### 5) Parte Meccanica - Pezzi da stampare in 3D

Guarda nella [cartella cad](../cad)

### 6) Parte Meccanica (per file V1) - Altro

Il materiale qui riportato vale per la versione 1 di Arlok. La versione 2 utilizzerá materiali diversi.

| Qt. | Descrizione |
| --- | --- |
| 12x | Vite M3 12mm (lunghezza filetto, ~15mm in totale) |
| 8x  | Vite M3 screw 6mm (lunghezza filetto, ~8mm in totale) |
| 14x | Rondella M3 (opzionale ma consigliate) |
| 12x | Dado M3 |
| 2x  | Vite M3, testa svasata, 8mm (lunghezza filetto,~10mm in totale) |
| 4x  | Distanziale esagonale F/F 8 o 10mm |
| 1x  | Ballcaster Tamiya 70144 (*) |
| 2x  | O-Ring, 70mm diametro interno, spessore 2-3mm (**) |

[Qui c'è una fotografia che illustra le viti necessarie](../media/arlok_screws_ita.jpg).

(*) Quando acquisti il ballcaster Tamiya 70144, ci sono pezzi per costruire 2 ball caster: potresti costruire un altro Arlok o darlo ad un amico così che lo costruisca anche lui! In alternativa puoi stampare in 3D il [Ball Caster V2 su Thingiverse](https://www.thingiverse.com/thing:1408935) con una'altezza di 30mm (Devi però saper usare [OpenScad](https://openscad.org/) per modificare il file .scad).

(**) Solo per i file 3D versione 1. Se stai la tua stampante è in grado di stampare il TPU, e stai usando la versione 1, potresti anche stampare un modello di pneumatico tra quelli messi a disposizione nella [cartella STL](../cad/v1/stl)  

### 7) Schede compatibili Arduino UNO R3 consigliate

Dal momento che lo shield di Arlok è stato disegnato utilizzando una normale board Arduino UNO come base, schede aventi componenti "alti" (come il connettore USB tipo B della Arduino UNO R3 originale), non possono essere utilizzate altrimenti "toccano" nella parte inferiore dello shield causando corto-circuiti e quindi notevoli danni. L'unico modo di utilizzare una scheda Arduino UNO R3 originale è quello di assemblare lo shield utilizzando degli header maschio da 15mm (non tanto comuni) oppure gli header passanti tipici di Arduino.  

Qui invece c'è un elenco di board "basse", compatibili, che non utilizzano il connettore USB-B:  

- [Keyestudio 328 Plus](https://amzn.to/3EVcUJO)
- [Cytron Maker UNO](https://www.cytron.io/p-maker-uno-simplifying-arduino-for-education)
- [Arduino Make Your UNO](https://store.arduino.cc/pages/make-your-uno-kit) 
- [Seeeduino 4.2](https://www.seeedstudio.com/Seeeduino-V4-2-p-2517.html)
- [Grove Beginner Kit](https://www.seeedstudio.com/Grove-Beginner-Kit-for-Arduino-p-4549.html)

Alcune delle schede elencate hanno il connettore di alimentazione di tipo Barrel Jack che pure è alto e può toccare sotto allo shield: il connettore in genere è di plastica quindi non causa corto circuiti, ma per sicurezza cerca di limare un po' le saldature sotto lo shield che possono toccare sul connettore e metti un pezzetto di nastro isolante per sicurezza.

### 8) Differenze tra PCB REV1 e prima release

- Aggiunto C7 per avere un po' di scorta di energia in più per componenti esterni
- Aggiunto un via (non collegato) vicino al GND dell'header di alimentazione, in caso fosse necessario riportare sullo shield la tensione VIN di Arduino
- Cambiata la serigrafia del connettore JSW da "POWER" a "LOGICS POWER" per non creare confusione dato che è utilizzato solo per la tensione dei 5V
- Aggiunto un via (not collegato) affianco al connettore JSW se vuoi utilizzare un interruttore a slitta a 3 pin (=un deviatore)
- Cambiato il trimmer VR1 dal tipo PT10LV10 (10x10mm) ad un tipo più piccolo (6x6mm)e facile da trovare. Ad ogni modo c'è comunque un via aggiuntivo collegato al pin centrale se hai già/vuoi utilizzare un trimmer da 10x10mm
- Aggiunta la serigrafia "A0" affianco a VR1 per ricordarsi dove è collegato il trimmer
- Estesa l'area di prototipazione (sono stati aggiunti altri 21 vias)
- Cambiata la serigrafia dei connettori a vite: è stato tolto il segno "-" e le scritte sono più leggibili
- Rimosso il logo OR e aggiunto quello di "Pizza Robotics - In pizza we crust" one

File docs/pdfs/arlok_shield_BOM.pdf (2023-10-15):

ARLOK

3d-printed Arduino Robot by @Cyb3rn0id at settorezero.com

https://www.github.com/settorezero/arlok

Arlok Shield REV1 components list

Part | Value | Notes
C1 | 100nF multilayer | 5mm pitch
C2 | 100nF multilayer | 5mm pitch
C3 | 1000µF 16V electrolytic | 3.5mm pitch - 8mm dia.
C4 | 100nF multilayer | 5mm pitch
C5 | 100nF multilayer | 5mm pitch
C6 | 100nF multilayer | 5mm pitch
C7 | 220µF 16V electrolytic | 2.5mm pitch – 6mm dia.
R1 | 15kΩ ¼W | BRO GRN ORN
R2 | 22kΩ ¼W | RED RED ORN
R3 | 330Ω ¼W | ORN ORN BRO
P1 | Tactile switch | 6x6mm - long pushbutton adviced
D1 | 1N4007 diode | Any 1N400x is good
P2 | Tactile switch | 6x6mm - long pushbutton adviced
RESET | Tactile switch | 6x6mm
VR1 | 5kΩ ÷ 20kΩ trimmer | 6x6mm
L1 | 3mm led
H1 | Male pinheader 10pin | See note (1)
H2 | Male pinheader 8pin | See note (1)
H3 | Male pinheader 5pin | See note (1)
H4 | Male pinheader 4pin | See note (1)
EXT | Male pinheader 7pin
EXT2 | Male pinheader 3pin
EXT3 | Male pinheader 3pin
EXT4 | Male pinheader 3pin
HC-SR04 | Male pinheader 4pin
I2C | Male pinheader 4pin | Optional
J1/COMM | Female pinheader 6pin
JP1 | Male pinheader 3pin+jumper
JSW/POWER | Male pinheader 2pin+jumper | Or 2.54mm pitch lever switch
LEFT_SERVO | Male pinheader 3pin
RIGHT_SERVO | Male pinheader 3pin
OLED | Female pinheader 4pin
X1 | Screw terminal 2pin | 5mm pitch
X2 | Screw terminal 2pin | 5mm pitch
GROVE | Grove male header | Optional

ARLOK

3d-printed Arduino Robot by @Cyb3rn0id at settorezero.com

https://www.github.com/settorezero/arlok

Notes

(1) Common male headers are 11mm long and have to be soldered from top of the shield with longer part going down toward the Arduino board. Those common headers are good only when you’re using a compatible Arduino UNO R3 board don’t having the USB type B connector and, preferably, don’t having the barrel jack connector. You can use the Arlok shield with common headers on adviced boards (some of them can require the barrel jack removing) or using it on genuine Arduino UNO R3 and similar but soldering longer headers (at least 15mm).

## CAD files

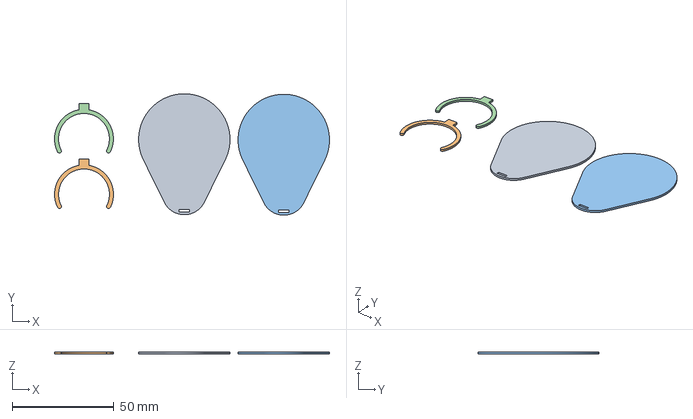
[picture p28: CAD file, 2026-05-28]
arduino/05_Huskylens/props/HeadsHuskylens.3mf
135.4 x 59.7 x 1.00 mm
HeadsHuskylens - head.step x 2
HeadsHuskylens - hook.step x 2

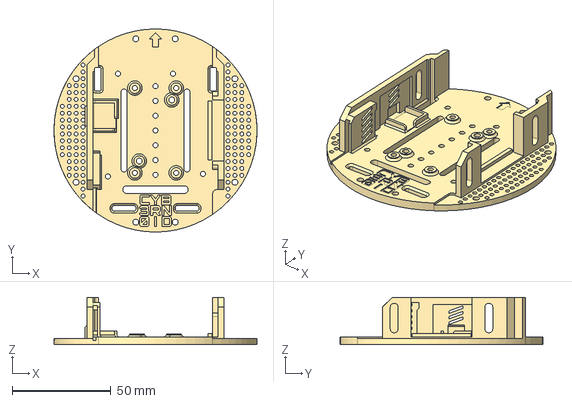
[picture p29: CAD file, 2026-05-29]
cad/v2/step/ArlokV2 - Upper Plate (engraved writing).step
102.9 x 103.0 x 24.0 mm

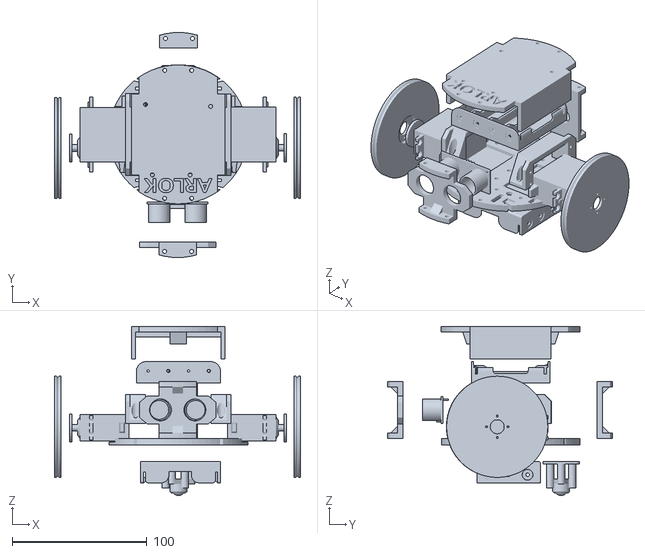
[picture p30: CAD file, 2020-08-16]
media/arlok_3d_exploded.stl
182.4 x 166.9 x 125.4

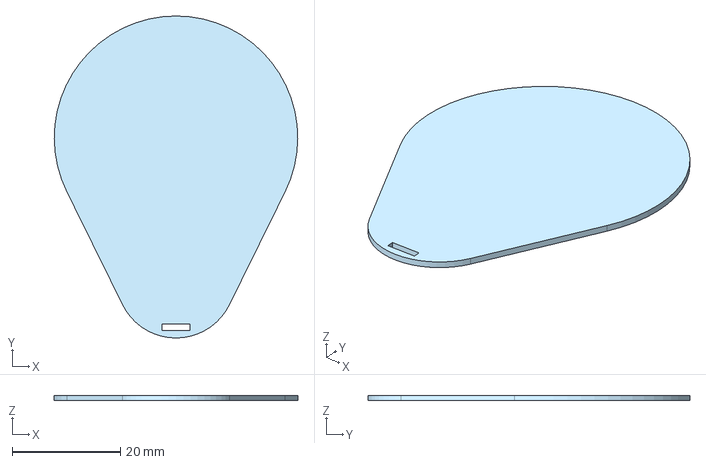
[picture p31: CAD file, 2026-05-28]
arduino/05_Huskylens/props/HeadsHuskylens - head.step
45.0 x 59.5 x 1.00 mm

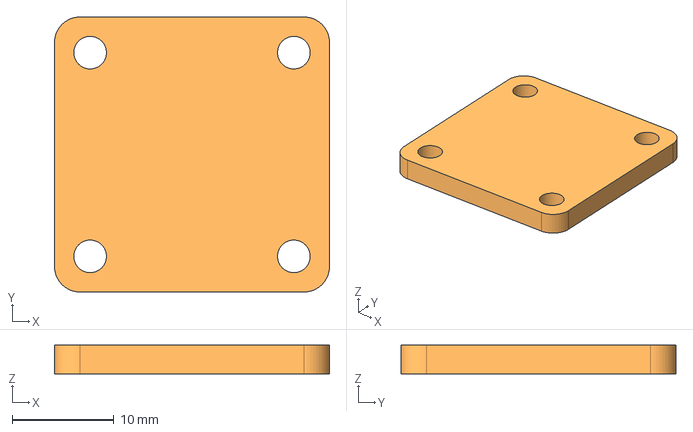
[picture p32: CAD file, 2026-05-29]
cad/v2/step/ArlokV2 - Spacer for 70144 Caster.step
27.0 x 27.0 x 2.80 mm

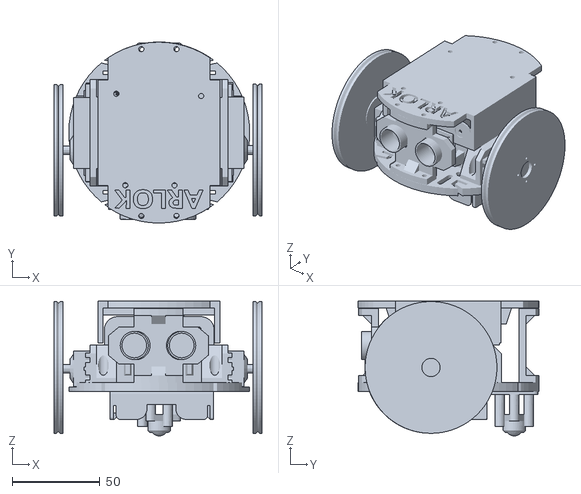
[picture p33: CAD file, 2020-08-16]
media/arlok_3d_view.stl
118.4 x 103.1 x 76.8

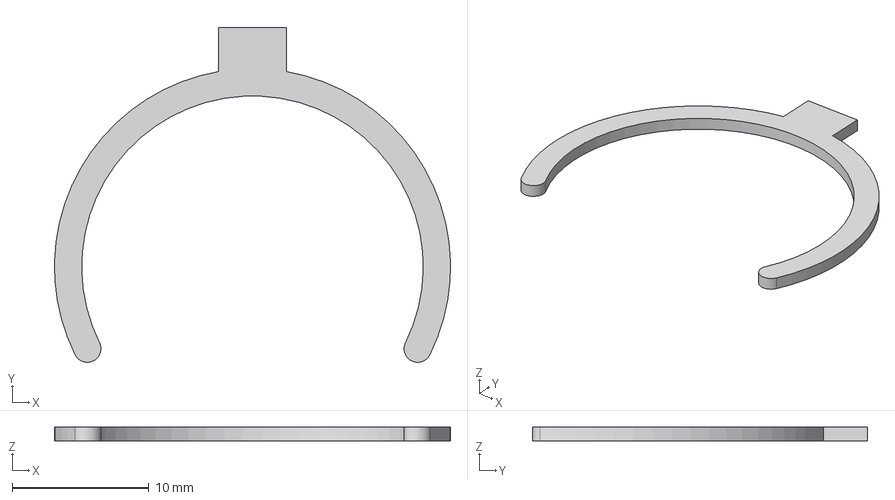
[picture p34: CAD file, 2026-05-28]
arduino/05_Huskylens/props/HeadsHuskylens - hook.step
29.0 x 24.5 x 1.00 mm

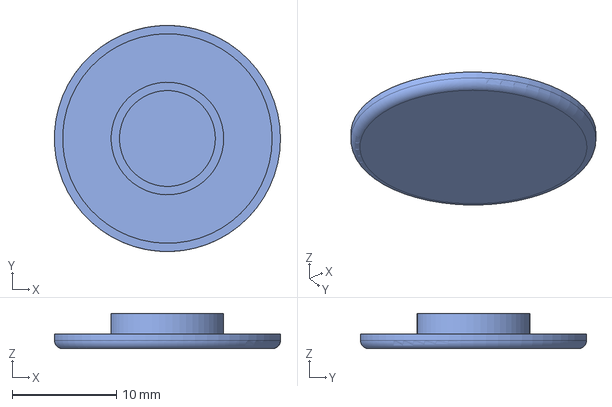
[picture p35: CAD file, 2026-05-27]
cad/v2/step/ArlokV2 - Hubcap (tight).step
21.7 x 21.7 x 3.40 mm

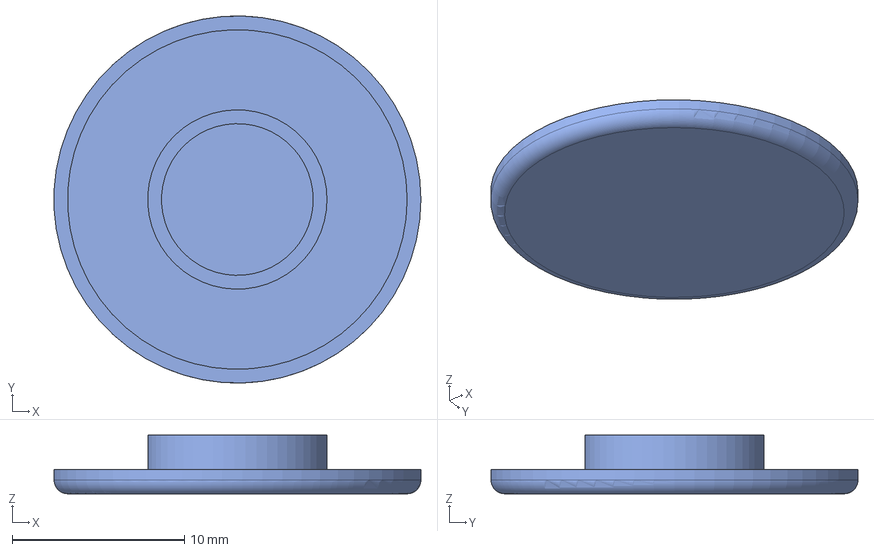
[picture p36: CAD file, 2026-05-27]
cad/v2/step/ArlokV2 - Hubcap.step
21.3 x 21.3 x 3.40 mm

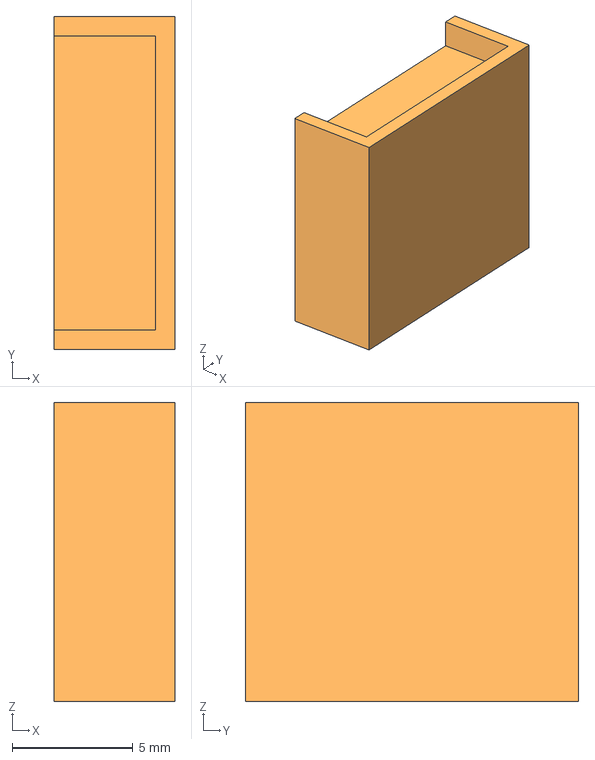
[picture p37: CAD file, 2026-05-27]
cad/v2/step/ArlokV2 - Oled Support.step
5.00 x 13.8 x 12.4 mm

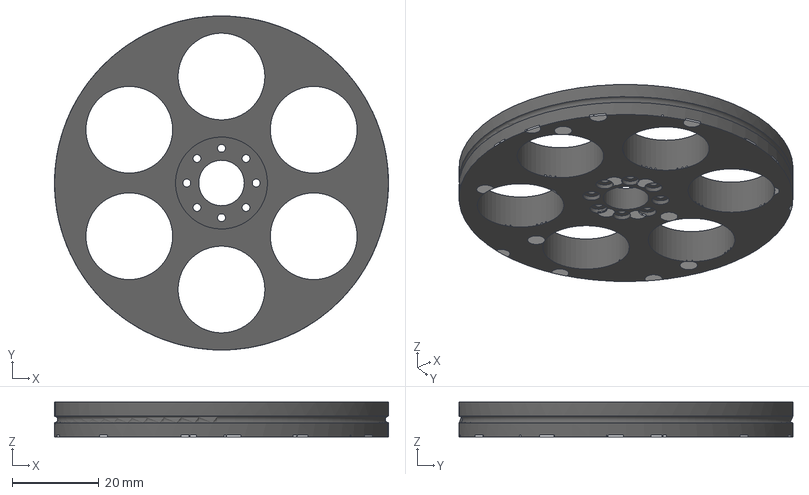
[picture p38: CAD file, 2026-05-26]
cad/v2/step/ArlokV2 Wheel - 6 circles (pois).step
77.0 x 77.0 x 8.00 mm

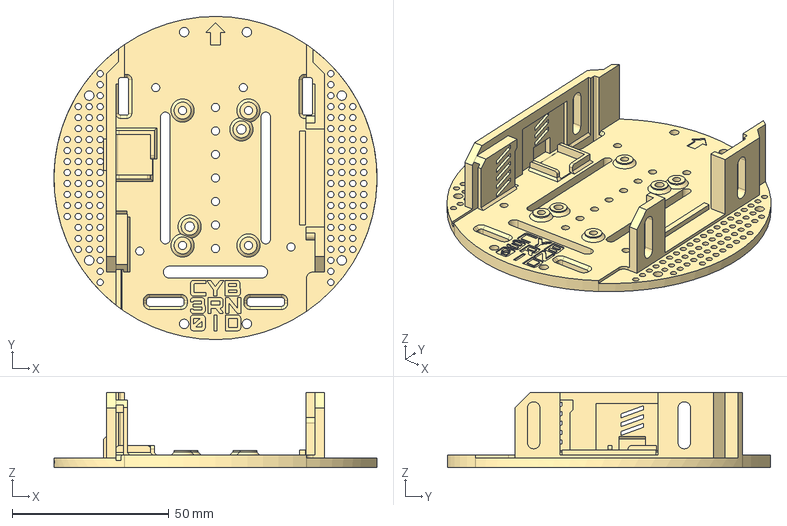
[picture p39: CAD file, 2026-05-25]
cad/v2/step/ArlokV2 - Upper Plate.step
102.9 x 103.0 x 24.0 mm

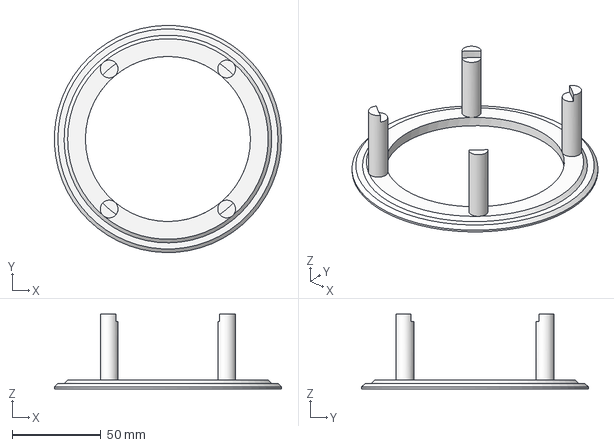
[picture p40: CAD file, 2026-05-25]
cad/v2/step/ArlokV2 - Pedestal.step
127.9 x 128.0 x 42.0 mm

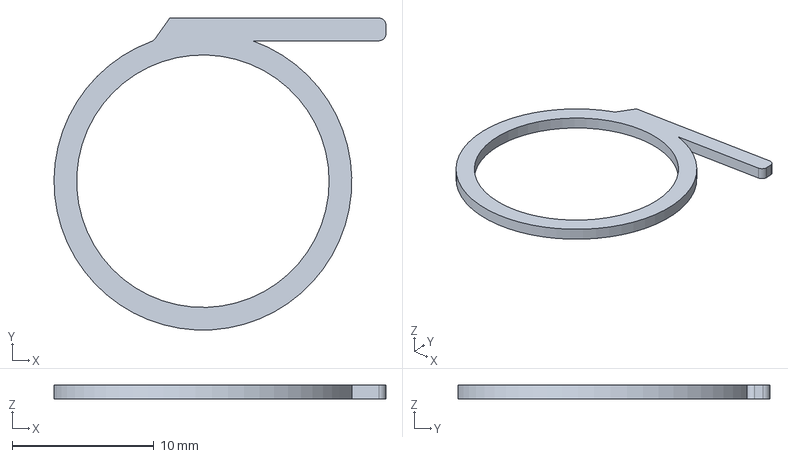
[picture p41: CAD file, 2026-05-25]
cad/v2/step/ArlokV2 moods - Brow.step
23.4 x 22.0 x 1.00 mm

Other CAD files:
cad/v2/step/ArlokV2 moods - Eyelashes.step
cad/v2/step/ArlokV2 moods - Contour.step
cad/v2/step/ArlokV2 moods - Unibrow.step
cad/v2/step/ArlokV2 moods - Sclera.step
arduino/05_Huskylens/props/HeadsHuskylens - head.stl
arduino/05_Huskylens/props/HeadsHuskylens - hook.stl
cad/v1/step/tires/arlok_tire_flat.step
cad/v1/step/wheels/arlok_wheel.step
cad/v1/step/wheels/arlok_wheel_slotted.step
cad/v1/step/wheels/arlok_wheel_star.step
cad/v1/step/wheels/arlok_wheel_star10.step
cad/v1/step/wheels/pizza_robotics/arlok_wheel_pizzarobotics.step
cad/v1/step/wheels/pizza_robotics/arlok_wheel_pizzarobotics_lid.step
cad/v1/stl/arlok_18650_holder.stl
cad/v1/stl/arlok_pillar_hole_(variant_06mm).stl
cad/v1/stl/arlok_pillar_hole_(variant_10mm).stl
cad/v1/stl/arlok_pillar_hole_(variant_12mm).stl
cad/v1/stl/arlok_pillar_sonar.stl
cad/v1/stl/arlok_pillar_sonar_(variant_rounded).stl
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

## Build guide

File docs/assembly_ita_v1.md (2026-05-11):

## Istruzioni montaggio ARLOK V1 in italiano

> Link rapido a questa pagina: [https://tinyurl.com/arlokmontaggio](https://tinyurl.com/arlokmontaggio)  

> Le misure delle viti sono espresse in millimetri e si riferiscono alla lunghezza della sola parte filettata, quindi testa esclusa

> ATTENZIONE: Questa guida passo-passo è stata pensata per il funzionamento di Arlok con le batterie AA dal momento che è il sistema più sicuro, ma ci sono [altri modi per far funzionare il robot](powering.md). Puoi anche, in seguito, [passare dalle batterie AA ad una 18650(lipo_mod_ita.md).

E' anche presente un [video su youtube](https://youtu.be/yHwYimkA6Dw) che illustra il montaggio passo-passo: si consiglia vivamente di vedere il video.

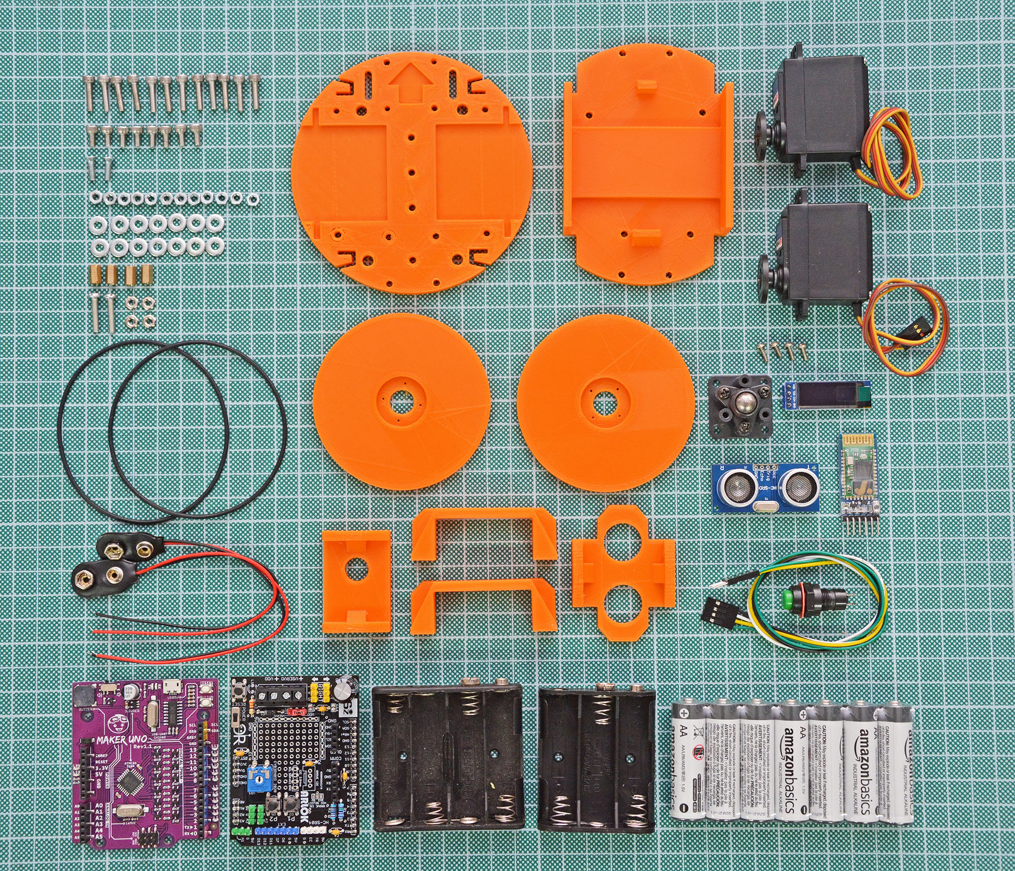
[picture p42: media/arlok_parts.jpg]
Arlok Parts
  

### Fasi preliminari

- Avete acquistato due servocomandi che ruotano a 360° oppure avete già modificato due normali servocomandi **analogici** per avere la rotazione continua (vedi [modifica dei servocomandi](servo_mod_ita.md) oppure [vedi questo video su youtube](https://www.youtube.com/watch?v=_Ubauj75d9E) )
- Avete già assemblato lo shield di Arlok
- Procuratevi alcune piccole fascette: torneranno utili per l'organizzazione dei cavi e per avere un risultato più pulito.

Aprite eventualmente la [Vista esplosa di ARLOK](./media/arlok_3d_exploded.stl) in una nuova finestra: vi tornerà molto utile per vedere come vanno posizionati ed orientati i pezzi.

Prendete la base (`arlok_plate_bottom`): la parte frontale-superiore è quella con la freccia e i due slot laterali. La freccia indica dove è posizionata la "faccia" del robot, ovvero quella con le capsule ultrasuoni.

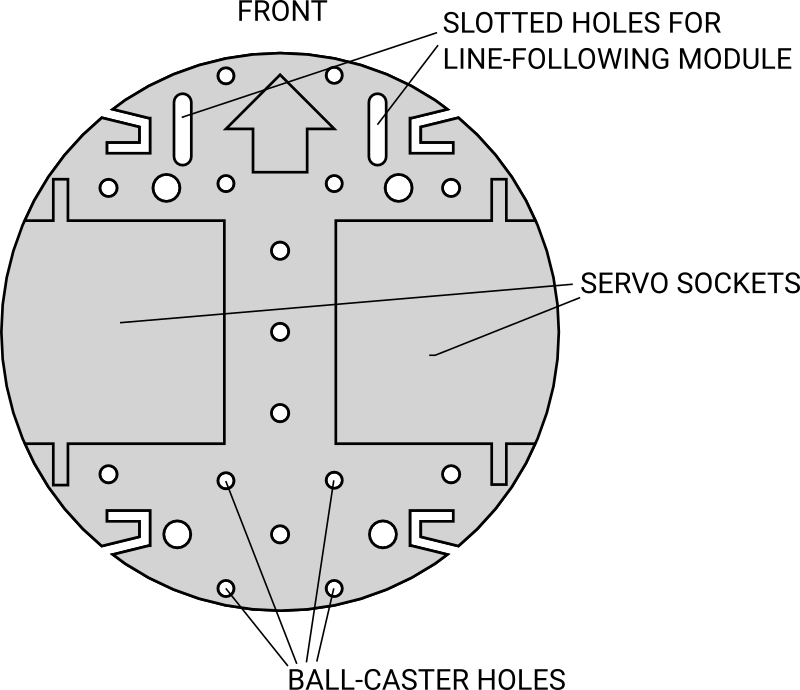
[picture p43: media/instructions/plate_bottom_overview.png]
Base Arlok


Gli incavi a forma di C o i fori più grandi possono essere utilizzati per far passare i vari cavi.

Gli step contrassegnati con un asterisco sono quelli che riguardano la sezione di alimentazione: sono illustrati gli step standard che prevedono l'utilizzo di batterie AA, che sono sicure. Se invece vuoi alimentare Arlok utilizzando una cella Lipo, c'è una guida a parte: [modifica per utilizzo 18650](lipo_mod_ita.md), per cui gli step con asterisco vanno saltati oppure eseguiti parzialmente facendo riferimento alla guida a parte.

### STEP 1 *

Agganciare il portabatterie per le 3 stilo sulla parte inferiore del piatto utilizzando 2 viti M3 da 8mm con testa svasata.  
La testa delle viti va chiaramente nel portabatterie e la vite fuoriesce sul lato superiore della base. Il portabatterie ha difatti i fori fatti per ospitare una vite a testa svasata che, entrando nell'incavo, non urta sulle batterie. Fissate le viti utilizzando due rondelline e 2 dadi M3.  

- Queste batterie sono utilizzate esclusivamente per alimentare la logica (ovvero la board Arduino ed eventuali accessori)  

### STEP 2

Posizionare i servocomandi negli appositi incavi presenti nella parte superiore della base. I servocomandi vanno orientati con l'asse di uscita rivolto in aventi.

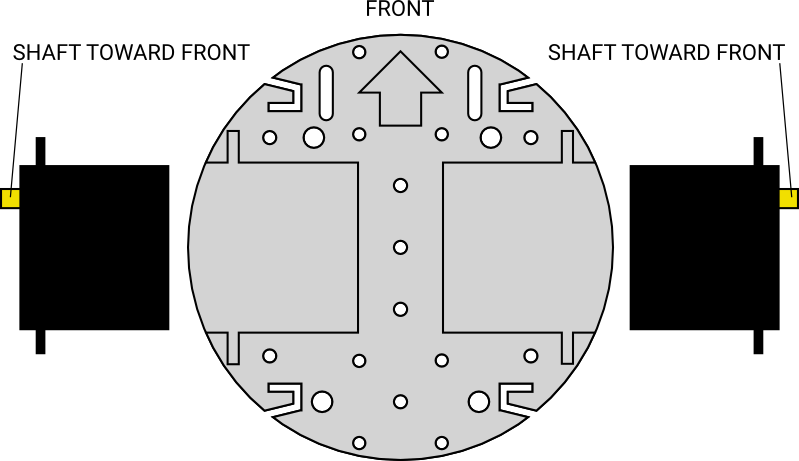
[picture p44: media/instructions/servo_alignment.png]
Posizionamento Servocomandi


Posizionare le staffe di bloccaggio dei servo al di sopra dei servo. (`arlok_servo_bracket`). Le "ali" di fissaggio dei servo vanno appoggiate sulla parte piatta delle staffe, senza usare viti. Le staffe vanno fissate sulla base utilizzando 4 viti M3 da 12mm a testa esagonale incavata. Nella parte inferiore avvitare con 4 dadi M3, utilizzare le rondelle.

Utilizzando un po' di nastro carta, annotare sui connettori dei servo qual'è il destro e qual'è il sinistro in modo da non commettere errori quando andremo a collegare i connettori dei servo sul PCB.

### STEP 3

Montare il Ball-Caster Tamiya 70144 seguendo le istruzioni presenti nella confezione dello stesso. Bisogna montare il Ball-Caster nella versione da 25mm 

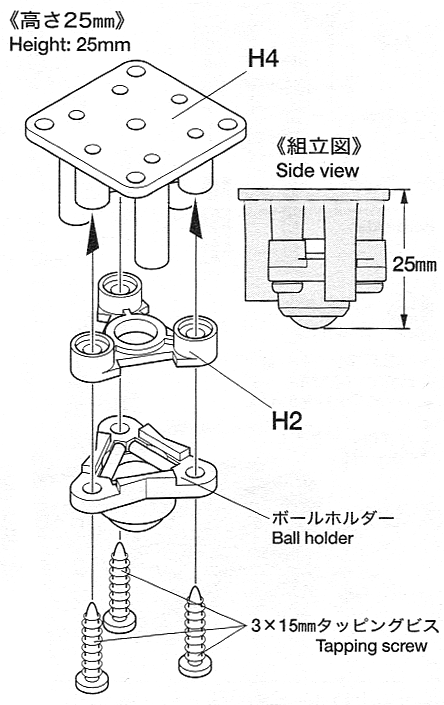
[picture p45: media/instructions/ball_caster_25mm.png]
Tamiya 70144 Ball-Caster


[Qui ci sono, eventualmente, le istruzioni complete del ball-caster](../media/instructions/ball_caster_instructions.png)

### STEP 4

Collegare il ball-caster alla base. Il ball caster va nella parte posteriore lato inferiore. Utilizzare 2 viti M3 12mm nei due buchi più vicini al centro lasciando liberi i 2 buchi posteriori: in questi buchi andrà difatti montato anche il pilastrino posteriore, per cui per ora vanno lasciati liberi. Utilizzare 2 dei dadi forniti col ball-caster.

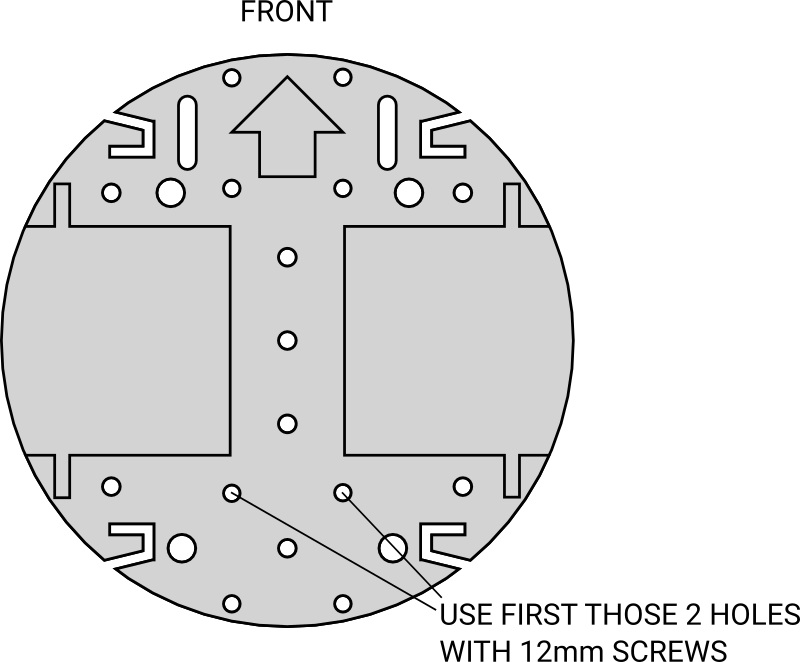
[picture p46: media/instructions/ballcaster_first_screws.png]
Viti ball-caster


Le viti vanno messe dall'alto verso il basso: avvitare in basso utilizzando 2 dadi M3.

### STEP 5

Montare il pilastrino posteriore (`arlok_pillar_hole_##`): è quello con il foro all'interno del quale va messo l'interruttore. Il foro va orientato verso il basso. Per fissare il pilastrino dovete utilizzare 2 delle viti più lunghe fornite insieme al ball caster (queste viti hanno la parte filettata lunga circa 14.5mm): le viti vanno infilate da pilastrino verso il basso e devono attraversare base e ball-caster ed essere quindi avvitate con 2 dadi dal lato del ball-caster. Qui non vanno utilizzate rondelle. Utilizzate 2 dadi forniti col ball-caster.

### STEP 6 *

Saldare 2 piccoli spezzoni di cavo ai terminali dell'interruttore che avete scelto. Infilare l'interruttore nel foro del pilastrino posteriore e fissarlo col dado fornito insieme all'interruttore stesso. Assicuratevi che l'interruttore sia in posizione OFF, magari utilizzando un tester in modalità "continuità": poggiando i puntali ai terminali dell'interruttore non deve suonare (OFF), se il tester suona vuol dire che il pulsante è ON.

### STEP 7

Montare il pilastrino per il sensore ultrasuoni (`arlok_pillar_sonar`) nella parte frontale: utilizzare 2 viti M3 12mm a testa esagonale incassata dal pilastrino verso il basso. Avvitare in basso con 2 dadi M3 e rondelle.

### STEP 8

Assemblate un cavetto sul sensore ultrasuoni seguendo questa video-guida: [https://youtu.be/iF_R0xU8K-4](https://youtu.be/iF_R0xU8K-4). Oppure, se non volete fare modifiche al sensore ultrasuoni, collgatelo allo shield utilizzando 4 normali cavetti jumper femmina/femmina di circa 12cm.

### STEP 9

Innestare il sensore ultrasuoni nel pilastrino frontale con l'header rivolto in basso.

### STEP 10

Prendere la piastra superiore (`arlok_plate_top`). La parte superiore-frontale è quella con la scritta ARLOK. Mettere 4 viti M3 6mm nei fori più al centro disposti secondo il layout di Arduino. Le viti vanno messe dal basso verso l'alto e nella parte superiore, filettata, vanno avvitati 4 distanziali esagonali femmina/femmina da 8 o 10mm.

### STEP 11

Appoggiare il portabatterie per le 4 stilo al di sopra delle staffe dei servocomandi: non è necessario fissarlo/incollarlo perchè rimarrà in posizione grazie alle ali laterali della base superiore. Collegare uno dei due fili dell'interruttore al filo nero del portabatterie e isolare il punto di giunzione. Se non l'avete fatto prima: assicuratevi che l'interruttore sia in posizione OFF. Mettere quindi le 4 batterie.

### STEP 12

Posizionare la piastra superiore con la scritta `ARLOK` va rivolta in avanti, ovvero in direzione delle capsule ultrasuoni. Far passare 4 viti M3 da 12mm dai fori in cima ai pilastrini attraverso la piastra, fissare le viti nella parte superiore con rondella e dado. Se le capsule ultrasuoni danno fastidio durante il passaggio delle viti nel pilastro anteriore, premerle verso dentro in modo da farle andare a filo e riportarle al di fuori una volta terminato il fissaggio.

### STEP 13

Posizionare la board Arduino sui distanziali e bloccarla con 4 viti M3 6mm.

### STEP 14 *

- Innestare lo shield di ARLOK sulla board Arduino
- Mettere il jumper `JP1` in posizione `VDD` (questo fa in modo che la logica sia alimentata dalle 3 batterie AA sul fondo del robot)
- Collegare i fili del sensore ultrasuoni sull'header contrassegnato come `HC-SR04` rispettando i segnali
- Collegare i connettori dei due servocomandi sugli headers rispettando l'orientamento LEFT (sinistro) / RIGHT (destro) e il colore dei fili (giallo o arandio=`S`, rosso=`+`, nero o marrone=`-`)
- Spostare l'interruttorino `POWER` dello shield verso il logo OR (=posizione OFF se lo avete saldato correttamente, ovvero senza coprire la scritta RESET)
- Mettere 3 batterie AA nel portabatterie inferiore
- Mettere i 2 fili dal portabatterie inferiore (3AA) nel terminale a vite contrassegnato come `VDD` : il filo rosso va in `+`. Se vedete il led `L1` accendersi, spostare l'interruttore `POWER` sullo shield nella direzione opposta in cui si trova
- Mettere i 2 fili dal portabatterie da 4 AA nel connettore a vite `VSERVO` : il filo rosso va in `+`. Se vedete i servocomandi muoversi o fare rumore, mettere l'interruttore sul pilastrino nella posizione opposta a quella in cui si trova.

### STEP 15

- Appoggiare le squadrette tonde dei servo nell'incavo della ruota con il perno verso il lato opposto. Guardare l'immagine per non sbagliare:

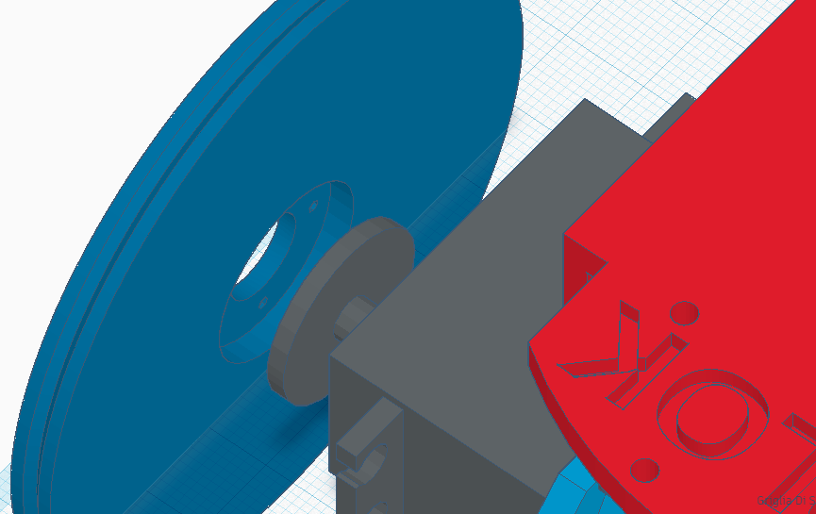
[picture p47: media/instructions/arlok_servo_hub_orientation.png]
orientamento servo
  
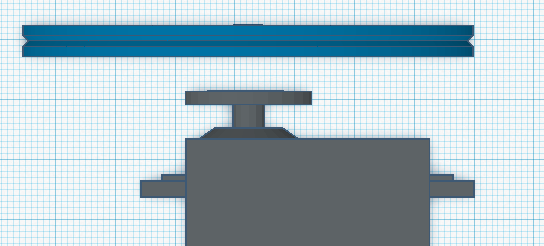
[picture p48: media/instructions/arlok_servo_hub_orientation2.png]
orientamento servo


- Le squadrette vanno fissate alle ruote utilizzando 2 delle piccole viti autofilettanti fornite con i servo. dall'esterno della ruota verso l'interno. La ruota ha già 4 piccoli buchini: usarne solo 2 posti a 180°. Bisogna applicare molta forza con un buon cacciavite per fare in modo che le viti si creino la filettatura nella plastica della ruota e della squadretta. La parte di vite che fuoriesce in genere non da problemi, ma se è troppo lunga e rischia di toccare sul servo, meglio tagliarla.
- Collegare quindi le ruote ai servo innestando il perno della squdretta sul perno del servo e fissarla utilizzando una vite, fornita coi servo, al centro della squadretta. 

### STEP 16

Posizionare gli O-Ring (o gli pneumatici stampati in 3D) sulle ruote.

### STEP 17

Caricare per primo il programma [explorer](../arduino/explorer). Come da descrizione riportata nel readme eseguire prima la procedura di setup per i servo: [potete seguire questo video](https://youtu.be/qzJxrcuSvpU).

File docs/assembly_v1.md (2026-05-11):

## ARLOK  V1 assembly Instructions

> Quick link to this page: [https://tinyurl.com/mountingarlok](https://tinyurl.com/mountingarlok)  

> 🇮🇹 For italian users: this guide is also available in italian language: [assembly - ITA](assembly_ita.md)  

> When you see the screw measure in millimeters: this is the length of the threaded part (without the head).

> NOTICE: This step-by step tutorial was thought for powering the robot with AA Batteries since is the safest way, but there are [other ways to power the robot](powering.md). You can also [change from AA batteries to 18650 cell](lipo_mod.md).  

There is a [video on youtube](https://youtu.be/yHwYimkA6Dw) showing the assemblying process. It's in italian language but video is very useful for understanding how certain parts must be placed correctly.

Arlok Parts  

### Preliminary Steps

- You've 2 servo having 360° rotation OR you have already modified the 2 servos for the continuous rotation (see [Servo modification guide](servo_mod.md) or see [this video on youtube](https://www.youtube.com/watch?v=_Ubauj75d9E))
- You've already assembled the Shield
- Take also some little cable ties: will turn useful for making a clean job.  

Open the [ARLOK exploded view](./media/arlok_3d_exploded.stl) in a new window: this will turn useful for seeing how parts must be placed/oriented.  

Take the base (`arlok_plate_bottom`): Front-top side is the one with the arrow and the 2 slotted holes. We will start from this piece.

Arlok plate bottom overview

You will use the big holes or the lateral "C" grooves for passing the cables.   

### STEP 1

Attach the 3AA-battery holder on the bottom of the plate using the 2x M3 8mm countersunk screws.  
Screws will go from bottom (head in the battery holder) to top so the nut will be on top of the base. Use 2 washers.
This battery will only power the logic board.

### STEP 2

Place the two servos in the grooves. The shaft will toward the front. 

Servo alignment

Place the brackets on the servos (`arlok_servo_bracket`). Attach servo brackets them using 4x M3 12mm Allen screws from top (head in the bracket) to bottom. On the bottom use 4x M3 washers and 4x M3 nuts.

Using a small piece of papertape write on Servo connectors "Right" and "Left" for remembering later where connects servo cables on the PCB. 

### STEP 3

Assemble the Tamiya 70144 ball-caster according instructions in the ball-caster box: You must assemble the ball-caster in the 25mm version:

Tamiya 70144 Ball-Caster

[Here are the ball-caster full instructions](../media/instructions/ball_caster_instructions.png)

### STEP 4

Attach the ball-caster on the bottom of the base, rear part. Use 2x M3 12mm Allen screws from top to bottom in the 2 holes near the center leaving free the 2 holes near the base border. 

First ball-caster screws

Nuts in the bottom part without washers. Use 2x M3 nuts provided with the ball-caster kit.

### STEP 5

Attach the rear pillar (`arlok_pillar_hole_##`): the one with the hole for the switch. The hole must go to the lower side. Use 2x of the longest M3 screws provided in the ball-caster kit (those screws have the lenght of threaded part of about 14.5mm): screws will pass from the  pillar through the base and ball-caster.
Nuts goes in the lower part. Don't use washers, use 2x M3 nuts provided with the ball-caster kit.

### STEP 6

Sold 2 small piece of wire on the round pushbutton (or the lever switch). Put the button in the hole of the rear pillar and fix it using his bolt. This pushbutton will detach the power from the 4AA batteries used for the servos. Check with a multimeter the pushbutton: must be in OFF position (opened).

### STEP 7

Attach the pillar for the ultrasonic sensor (`arlok_pillar_sonar`) to the base using 2x M3 12mm Allen screws from top to bottom. Nuts in the lower part. Use washers.

### STEP 8

Straight the male pinheader of the ultrasonic sensor and attach 4 female to female jumpers (wire must be long at least 12-15cm). Mind the colors you've used for the ultrasonic sensor signals: red wire for the `Vdd`, black for `Gnd` and other 2 different colors for `echo` and `trigger`. I've prepared an italian video-guide for using certain male/female 4pin cable, maybe this can be another idea for you for attaching the sonar: [https://youtu.be/iF_R0xU8K-4](https://youtu.be/iF_R0xU8K-4)

### STEP 9

Insert the ultrasonic sensor in the pillar with cables on the bottom.

### STEP 10

Take the top plate (`arlok_plate_top`). The front-top part is the one with the ARLOK writing on it. Put 4x M3 6mm screws in the central holes having the Arduino layout, from bottom to top. Screw the 4x M3 8 or 10mm female/female spacers on the screws.

### STEP 11

Place the 4AA battery holder on the servo brackets. It's no needed to attach it since will be held from the lateral wings of the top plate. Sold one wire of the pushbutton to the negative wire of the 4AA battery holder. Be sure pushbutton is in the OFF position (eventually check with a multimeter) and then put in 4 AA batteries.

### STEP 12

Put the top plate on the bottom assembly, with the ARLOK writing in the same direction of the ultrasonic sensor. Fix the top plate using 4x M3 12mm screws from the bottom of pillars through the plate and 4x M3 bolts with washers.

### STEP 13

Put the MakerUNO on the spacers. Attach the board using the 4x M3 6mm screws.

### STEP 14

- Attach the ARLOK shield on top of the Arduino board
- Put the `JP1` jumper in the `VDD` position (logic powered from the 3AA battery)
- Attach the wires from the ultrasonic sensor on the `HC-SR04` header respecting signals/colors.
- Attach the 2 servo connectors on the Servo headers respecting the LEFT-RIGHT arrows and the wire colors (orange=`S`, red=`+`, brown=`-`)
- Move the small `POWER` switch on the shield toward the OR logo (OFF position if you soldered it correctly without covering the RESET writing).
- Put 3 AA batteries in the battery holder
- Put the 2 wires from the 3xAA battery holder in the `VDD` screw terminal, red wire in the `+`. If you see the `L1` led turning on, move the `POWER` switch on the shield in the opposite position.
- Put the 2 wires from the 4xAA battery holder in the `VSERVO` screw terminal, red wire in the `+`. If you see servo moving, push the button/turn the lever.

### STEP 15

- Attach the round servo hub in the groove of the wheels using 2 self-tapping screws coming from the servo kit. Screw heads will go outside (part of the wheel without the grove). The notch of the hubs will go toward the servo shaft. Follow the pictures:

servo hub orientation  
servo hub orientation

- Attach the wheels to the servos using the small self-tapping screws from the servo kit through the horn.

### STEP 16

Place the O-Ring on the wheels.

### STEP 17

Load first the [explorer example](../arduino/explorer). Read the readme document in the folder for doing the setup procedure. [Here is an italian guide about the setup procedure](https://youtu.be/qzJxrcuSvpU).

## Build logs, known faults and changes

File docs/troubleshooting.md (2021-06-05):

## ARLOK troubleshooting

How to resolve common problems with ARLOK

> Quick link to this page: [https://tinyurl.com/troubleshootingarlok](https://tinyurl.com/troubleshootingarlok)

1) [ARLOK doesn't turn or doesn't move](#movement)
2) [ARLOK make too little or too big movement while turning](#turning)
3) [ARLOK goes backward too far or too little](#backward)
4) [Can't upload code (stk500_getsync() error)](#getsync)

###  ARLOK doesn't turn or doesn't move

Servos are driven by an impulse. Don't forget we're using modified servos, so an impulse of about 1500mS means servo stopped (a normal servo will turn to 90 degrees), an impulse less than 1500mS will make servo moving to a direction, an impulse greater than 1500mS will make servo moving in opposite direction.   

ARLOK movement is based on a central position (default 1500mS, the setup procedure is used for modifying this value) ± a constant value: ARLOK moves forward or backward using an impulse of (1500mS ± `SPEED`) or turns left or right using an impulse of (1500mS ± `SPEED_SLOW`).  

`SPEED` and `SPEED_SLOW` are defined in the source code, by default:

```
#define SPEED  600 // normal speed for forward moving (center point+speed microseconds)
#define SPEED_SLOW 125 // speed used for maneuvers
```

If ARLOK cannot move forward or backwards then raise the value assigned to `SPEED`, example:

```
#define SPEED  700
```

If ARLOK cannot turn left or right raise the value assigned to `SPEED_SLOW`, example:

```
#define SPEED_SLOW  200
```

###  ARLOK make too little or too big movement while turning

The amount of movement during a turn is defined by the `TURN_TIME` value. This value is expressed in milliseconds. By default this value is 600 (ARLOK will make the movement to left of right for 0.6 second):

```
#define TURN_TIME 600 // amount of time used for turning, change this if turning angle is not 90 degrees
```

If movement of a turn is less than 90 degree, raise this value. Example:

```
#define TURN_TIME 1000 
```

If movement of a turn is greater than 90 degree, lower this value. Example:

```
#define TURN_TIME 500 
```

###  ARLOK goes backward too far or too little

The amount of movement moving backward by the `BACK_TIME` value. This value is expressed in milliseconds. By default this value is 500 (ARLOK will go backward for 0.5 second):

```
#define BACK_TIME 500 // amount of time used for going backward after robot found an obstacle
```

If movement backward is too large, lower this value. Example:

```
#define BACK_TIME 400 
```

If movement backward is too small, raise this value. Example:

```
#define BACK_TIME 700 
```

###  Can't upload code (stk500_getsync() error)

Probably you've the bluetooth module attached

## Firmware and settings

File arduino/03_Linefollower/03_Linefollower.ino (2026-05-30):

/*
 * ARLOK
 * Educational Robot based on Arduino UNO
 * (c)2020-2026 Giovanni Bernardo (https://www.settorezero.com)
 * 
 * LINE FOLLOWER DEMO
 *
 * https://www.github.com/settorezero/arlok
 * 
 *
 * LICENSE
 * Attribution-NonCommercial-ShareAlike 4.0 International 
 * (CC BY-NC-SA 4.0)
 * 
 * This is a human-readable summary of (and not a substitute for) the license:
 * You are free to:
 * 
 * SHARE - copy and redistribute the material in any medium or format
 * ADAPT -  remix, transform, and build upon the material
 * The licensor cannot revoke these freedoms as long as you follow the license terms.
 * Under the following terms:
 * ATTRIBUTION -  You must give appropriate credit, provide a link to the license, 
 * and indicate if changes were made. You may do so in any reasonable manner, 
 * but not in any way that suggests the licensor endorses you or your use.
 * NON COMMERCIAL -  You may not use the material for commercial purposes.
 * SHARE ALIKE -  If you remix, transform, or build upon the material,
 * you must distribute your contributions under the same license as the original.
 * NO ADDITIONAL RESTRICTIONS - You may not apply legal terms or technological 
 * measures that legally restrict others from doing anything the license permits.
 * 
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
 * Please read the Full License text at the following link:
 * https://creativecommons.org/licenses/by-nc-sa/4.0/legalcode
 *  
 * CREDITS
 * 
 * Adafruit
 * Because makes a lot of coll and useful libraries - please consider buying something from Adafruit
 *
 * Steve Garrat
 * For the idea about using HC-SR04 sonar on interrupts:
 * (https://homediyelectronics.com/projects/arduino/arduinoprogramminghcsr04withinterrupts/)
 * 
 * Nick Bontranger
 * For the library allows using servo on Timer 2
 * https://github.com/nabontra/ServoTimer2
 * 
 * LIBRARIES TO INSTALL:
 * - Adafruit SSD1306 by Adafruit
 * - Adafruit GFX by Adafruit
 * - TimerOne by Jesse Tane, Jérôme Despatis, Michael Polli, Dan Clemens, Paul Stoffregen
 * - ServoTimer2 : This one requires manual installation (copy the folder in Documents\Arduino\Libraries) => https://github.com/nabontra/ServoTimer2
 * 
 */

#include <SPI.h>
#include <Wire.h>
#include <Adafruit_GFX.h>
#include <Adafruit_SSD1306.h>
#include <TimerOne.h> // Library for Timer1 Interrupts
#include <ServoTimer2.h> // Library for using servo on Timer 2
#include <EEPROM.h> // Library for Arduino internal eeprom memory

// ****************** LIPO BATTERY STUFF
//#define LIPO // uncomment if you're using the LiPo battery
#define LIPO_PIN    A2  // analog pin where the 18650 is attached for checking voltage
#define BAT_AVG     32  // averages on battery readings
#define BAT_DIV     .005180840664F // .00488758553274F

// ****************** GPIO DEFINITIONS
#define MotorRPin   9   // signal for right servomotor
#define MotorLPin   10  // signal for left servomotor
#define P1          2   // pushbutton P1 on ARLOK PCB ('button' on MakerUNO board)
#define P2          5   // pushbutton P2
#define trigPin     4   // HC-SR04 - trigger
#define echoPin     3   // HC-SR04 - echo
#define buzzer      8   // buzzer on MakerUNO
#define linemodule  A1  // line follower module

// ****************** SERVO STUFF
ServoTimer2 MotorL;               // left servomotor object
ServoTimer2 MotorR;               // right servomotor object
uint16_t servoL_center = 1500;    // default value for left servomotor center point
uint16_t servoR_center = 1500;    // default value for right servomotor center point
uint16_t servoL_balanced;         // left servomotor balanced center point
uint16_t servoR_balanced;         // right servomotor balanced center point
int16_t servo_balance = 0;        // default value for servomotors balancing of the center point
uint8_t servoL_eeprom = 0;        // eeprom memory location for storing point zero of left servomotor
uint8_t servoR_eeprom = 2;        // eeprom memory location for storing point zero of right servomotor
uint8_t servo_balance_eeprom = 4; // eeprom memory location for storing the balacing of servomotors

// CHECK/CHANGE THOSE VALUES IF YOU'VE PROBLEMS with Robot movements!
#define SPEED       140           // normal speed for forward moving (center point+speed microseconds), rise this if your robot doesn't move
#define ACCEL_STEP    6           // increment ramp
#define SPEED_DIV     7           // speed divisor (computed speed will be divided by this value)
#define LINECENTER   500	      // Sensor value for line positioned at center
#define HYSTERESIS   100         // difference between a line point and another: phisically is 200 but keep it lower

// stuff used by sonar
#define TIMER_US      50         // Timer1 interrupt every 50uS
#define TICK_COUNTS 4500         // 4500*50uS = 225mS, time space between two consecutive trigger pulses
#define OBSTACLE       4         // ARLOK will stop if an obstacle is nearer than this

// stuff used by oled display
#define SCREEN_WIDTH  128
#define SCREEN_HEIGHT  32
#define OLED_RESET     -1
Adafruit_SSD1306 display(SCREEN_WIDTH, SCREEN_HEIGHT, &Wire, OLED_RESET);

// Global variables
volatile long distance = 0;       // distance measured by sonar, cm
uint8_t maneuver=0; // actual maneuver
uint8_t maneuverp=0; // previous maneuver

// enum used for ARLOK working mode
enum arlok_mode 
 {
 configuration,
 normal
 };
arlok_mode mode=normal;  // actual mode

// enum used for config menu pages on display
enum config_pages 
 {
 left_motor = 0,
 right_motor = 1,
 balance = 2,
 config_end = 3
 };

void setup(void) 
 {
 // sonar setup
 pinMode(trigPin, OUTPUT);
 pinMode(echoPin, INPUT);
 
 // servomotors setup
 MotorL.attach(MotorLPin);
 MotorR.attach(MotorRPin);
 
 // pushbuttons setup
 pinMode(P1, INPUT_PULLUP);
 pinMode(P2, INPUT_PULLUP);
 
 // buzzer setup (if present)
 #ifdef buzzer
  pinMode(buzzer, OUTPUT);
  digitalWrite(buzzer, LOW);
 #endif
 
 move_stop(100);
 
 // interrupts
 Timer1.initialize(TIMER_US); // Initialise timer 1
 Timer1.attachInterrupt(timer1_ISR); // Attach interrupt to the timer service routine
 attachInterrupt(digitalPinToInterrupt(echoPin), sonarEcho_ISR, CHANGE); // Attach interrupt to the sensor echo input

 delay(500);
 Serial.begin(9600);  // the HC-05 in normal mode (no AT) works at 9600baud (38400 if in AT)
 randomSeed(analogRead(3));  // start-up random number generator using an unused analog input

 // SSD1306_SWITCHCAPVCC = generate display voltage from 3.3V internally
 if (!display.begin(SSD1306_SWITCHCAPVCC, 0x3C)) 
  {  // Address 0x3C for 128x32
  Serial.println(F("SSD1306 allocation failed"));
  while (1);  // Don't proceed, loop forever
  }
  
 display.clearDisplay();
 display.setTextSize(2);
 display.setTextColor(SSD1306_WHITE, SSD1306_BLACK);

 // center values used for servomotors, loaded from eeprom
 // if in the eeprom are saved values out of the range 500-2500, 1500 will be used
 // (this happens when eeprom memory was never used since contains 0xFFFF value)
 uint16_t LV = EEPROM.read(servoL_eeprom) << 8;
 LV |= EEPROM.read(servoL_eeprom + 1);
 uint16_t RV = EEPROM.read(servoR_eeprom) << 8;
 RV |= EEPROM.read(servoR_eeprom + 1);
 if (LV < 2501 && LV > 499) servoL_center = LV;
 if (RV < 2501 && RV > 499) servoR_center = RV;
 // balance value used for fine tuning of differences in speed of the servomotors
 // the range is based on the value set in the SPEED constant
 int16_t BL = EEPROM.read(servo_balance_eeprom) << 8;
 BL |= EEPROM.read(servo_balance_eeprom + 1);
 if (BL > -SPEED && BL < SPEED) servo_balance = BL;
 balance_servos();
 move_stop(100);

 display.setTextSize(2);
 display.setCursor(0, 0);
 
 // if P1 is pressed during the setup function, I'll start the setup mode
  if (digitalRead(P1) == 0) 
   {
   mode = configuration;
   Serial.println("Setup mode");
   while (digitalRead(P1) == 0) {continue;}
   }
 } // \setup()

void loop() 
 {
 static boolean juststarted=true;
 static uint16_t lastRval=0;
 static uint16_t lastLval=0;
 #ifdef LIPO
  static uint8_t bat_count=0;
  static float bat_val=0;
  static float bat_now=0;
 #endif
 
 while (mode==configuration) config_menu();
 
 display.clearDisplay();
 display.setTextSize(2);
 display.setCursor(0, 0);
  
 if (juststarted) 
   {
   move_stop(100);
   display.println("Press P1");
	display.print("to start");
   display.display();
   while(digitalRead(P1));
	display.clearDisplay();
   display.print("starting");
   display.display();
	delay(1000);
   juststarted = false;
	display.clearDisplay();
   display.display();
   }
 
 int16_t linePosition = analogRead(linemodule);
 display.setCursor(0, 0);
 char buffer[6];
 sprintf(buffer, "%04d ", linePosition);
 display.print(buffer);
 
 // Print battery value on second row if enabled 
 #ifdef LIPO
  // read battery
  bat_val+=analogRead(LIPO_PIN);
  bat_count++;
  if (bat_count==BAT_AVG)
     {
     bat_val/=BAT_AVG;
     bat_now=bat_val*BAT_DIV;
     bat_val=0;
     bat_count=0;
     }
  display.setCursor(0,17);
  display.print("Bat:");
  display.print(bat_now);
  display.print("V");
 #else
  display.setCursor(0,17);
  display.print("LineFollow");
 #endif
 
 display.setCursor(62,0);
 if(linePosition > 980) // line is detected from all sensors
    {
    display.print("|||||");
    move_stop(1000);
    }
 else if(linePosition < 50) // line not detected from any sensor
    {
    display.print(".....");
    move_forward(lastLval-1,lastRval-1);
    }
 else    // not all sensors ar seeing the line but one or more
    {
    // calculate offset from the center of sensor
    int centerOffSet = linePosition - LINECENTER;
	// if centerOffSet is into the center death zone go forward
    if(abs(centerOffSet) <= HYSTERESIS)
        {
        display.print("..|..");
        move_forward(SPEED/SPEED_DIV,SPEED/SPEED_DIV);
        }
    else
        {
        int motorLeftSpeed = 0;
        int motorRightSpeed = 0;
        volatile float ds=(float(abs(centerOffSet))/float(LINECENTER))*float(SPEED);
        if(centerOffSet < 0) // left sensor active, must give more power to right motor
            {
            display.print("||...");
            motorLeftSpeed = SPEED - ds;
            motorRightSpeed = SPEED + ds;
            }
        else
            {
            display.print("...||"); // right sensor active, must give more power to left motor
            motorLeftSpeed = SPEED + ds;
            motorRightSpeed = SPEED - ds;
            }
        move_forward(motorLeftSpeed / SPEED_DIV, motorRightSpeed / SPEED_DIV);
        lastLval=motorLeftSpeed/SPEED_DIV;
        lastRval=motorRightSpeed/SPEED_DIV;
        }
    }
    
    display.display();
    
	
    if (distance<OBSTACLE)
      {
      move_stop(50);
      sound();
      delay(1000);
      }
      
 } // \loop

void config_menu(void) 
 {
 static config_pages actual_page=left_motor;
 static bool splash = true;

 if (splash) 
    {
    display.setCursor(0, 0);
    display.println("SETUP");
    display.display();
    delay(2000);
    display.clearDisplay();
    display.setCursor(0, 0);
    display.display();
    splash = false;
    delay(1000);
    }

 uint16_t val = analogRead(0);
 // mapping 0-1023 to 500-2500
 uint16_t pos = map(val, 0, 1023, 500, 2500);
 // mapping 0-1023 to SPEED, -SPEED
 int16_t balance_pos = map(val, 0, 1023, SPEED, -SPEED);
 String pre_balance_txt = balance_pos > 0 ? "   " : "L< ";
 String post_balance_txt = balance_pos < 0 ? "   " : " >R";

 switch (actual_page) 
    {
    case left_motor:  // left servomotor setup
      display.setCursor(0, 0);
      display.setTextSize(1);
      display.print("LEFT MOTOR (");
      display.print(servoL_center);
      display.println(")");
      display.setTextSize(2);
      display.print(pos);
      display.print("  ");
      display.println();
      display.setTextSize(1);
      display.print("P1: save P2: next");
      display.display();
      MotorL.write(pos);
      break;

    case right_motor:  // right servomotor setup
      display.setCursor(0, 0);
      display.setTextSize(1);
      display.print("RIGHT MOTOR (");
      display.print(servoR_center);
      display.println(")");
      display.setTextSize(2);
      display.print(pos);
      display.print("  ");
      display.println();
      display.setTextSize(1);
      display.print("P1: save P2: next");
      display.display();
      MotorR.write(pos);
      break;

    case balance:  // balancing setup
      display.clearDisplay();
      display.setCursor(0, 0);
      display.setTextSize(1);
      display.print("SERVOS BALANCE (");
      display.print(servo_balance);
      display.println(")");
      display.setTextSize(2);
      display.print(pre_balance_txt);
      display.print(balance_pos);
      display.println(post_balance_txt);
      display.setTextSize(1);
      display.print("P1: save P2: next");
      display.display();
      MotorL.write(servoL_center);
      MotorR.write(servoR_center);
      break;

    case config_end:
      display.setTextSize(2);
      display.setCursor(0, 0);
      display.println("P1: Exit");
      display.println("P2: Return to Setup");
      display.display();
      break;
    }  // switch

 // P1 pressed: confirm value or exit from menu
 if (digitalRead(P1) == 0) 
    {
    delay(50);
    if (digitalRead(P1)==0) 
	      {
        while (digitalRead(P1) == 0) {continue;}
        switch (actual_page)
		        {
            case left_motor:
              servoL_center = pos;
              // I must split the 16bit value in two bytes
              // and save values in 2 different EEPROM locations
              EEPROM.update(servoL_eeprom, (uint8_t)(pos >> 8));
              delay(4);  // an eeprom.write takes 3.3mS
              EEPROM.update(servoL_eeprom + 1, (uint8_t)(pos & 0x00FF));
              delay(4);
              Serial.print("Left zero: ");
              Serial.println(pos);
              break;

            case right_motor:
              servoR_center = pos;
              // I must split the 16bit value in two bytes
              // and save values in 2 different EEPROM locations
              EEPROM.update(servoR_eeprom, (uint8_t)(pos >> 8));
              delay(4);  // an eeprom.write takes 3.3mS
              EEPROM.update(servoR_eeprom + 1, (uint8_t)(pos & 0x00FF));
              delay(4);
              Serial.print("Right zero: ");
              Serial.println(pos);
              break;

            case balance:
              servo_balance = balance_pos;
              EEPROM.update(servo_balance_eeprom, (balance_pos >> 8));
              delay(4);  // an eeprom.write takes 3.3mS
              EEPROM.update(servo_balance_eeprom + 1, (balance_pos & 0x00FF));
              delay(4);  // an eeprom.write takes 3.3mS
              Serial.print("Balance pos: ");
              Serial.println(balance_pos);
              balance_servos();
              break;

            case config_end:
              // exit from menu
              mode = normal;
              display.clearDisplay();
              display.display();
              Serial.println("Config exit");
              return;
            break;
            } // \switch actual_page
        } // \P1 pressed for sure
    } // \P1 pressed

 // P2 pressed: change the page
 if (digitalRead(P2) == 0) 
    {
    delay(50);
    if (digitalRead(P2) == 0) 
	    {
        while (digitalRead(P2) == 0) {continue;}
        // the C++ deals with enums as an independent type
        // so we must convert it in an integer if we want to use the ++ operator
        uint8_t tmp = (uint8_t)actual_page;
        tmp++;
        if (tmp > (uint8_t)config_end) tmp = 0;
        actual_page = (config_pages)tmp;
        display.clearDisplay();
        display.display();
        delay(10);
        } // \P2 pressed for sure
    } // \P2 pressed
 } // \config_menu()

void sound(void) 
 {
 uint8_t i = 30;
 while (i--) 
    {
    #ifdef buzzer
     digitalWrite(buzzer, HIGH);  // turn on the buzzer
     delayMicroseconds(2000);
     digitalWrite(buzzer, LOW);  // turn off the buzzer
     delayMicroseconds(2000);
    #endif
    }
 } // \sound()

void balance_servos(void) 
 {
 if (servo_balance < 0) 
    {
    servoL_balanced = servoL_center;
    servoR_balanced = servoR_center + abs(servo_balance);
    } 
 else if (servo_balance > 0) 
    {
    servoL_balanced = servoL_center - servo_balance;
    servoR_balanced = servoR_center;
    } 
 else 
   {
   servoL_balanced = servoL_center;
   servoR_balanced = servoR_center;
   }

  Serial.print("ServoL_balanced:");
  Serial.println(servoL_balanced);
  Serial.print("ServoR_balanced:");
  Serial.println(servoR_balanced);
 } // \balance_servos()


// moves forward giving different speed for left and right motors
void move_forward(uint16_t speedL, uint16_t speedR)
 {
 maneuver=1;
 static uint16_t currentSpeedL=ACCEL_STEP;
 static uint16_t currentSpeedR=ACCEL_STEP;
 static uint16_t speedLP=ACCEL_STEP;
 static uint16_t speedRP=ACCEL_STEP;
 if (speedL>SPEED) speedL=SPEED;
 if (speedR>SPEED) speedR=SPEED;
 
 if (maneuver!=maneuverp)
   {
   maneuverp=maneuver;
   speedLP=speedL;
   speedRP=speedR;
   currentSpeedL=ACCEL_STEP;
   currentSpeedR=ACCEL_STEP;   
   }
 else 
   {
   if (speedL!=speedLP)
      {
      if (speedL<speedLP)
         {
         currentSpeedL=speedL;
         }
      else
         {
         currentSpeedL=speedLP; 
         }
      speedLP=speedL;
      }
 
   if (speedR!=speedRP)
      {
      if (speedR<speedRP)
         {
         currentSpeedR=speedR;
         }
      else
         {
         currentSpeedR=speedRP;   
         }
      speedRP=speedR;
      }
   }

 // ramp L
 if (currentSpeedL < speedL)
    {
    currentSpeedL+=ACCEL_STEP;
    if (currentSpeedL > speedL) currentSpeedL = speedL;
    }
 // ramp R
 if (currentSpeedR < speedR)
    {
    currentSpeedR+=ACCEL_STEP;
    if (currentSpeedR > speedR) currentSpeedR = speedR;
    }
 MotorL.write(servoL_balanced + currentSpeedL);
 MotorR.write(servoR_balanced - currentSpeedR);
 //delay(1);
 return;
 }
 
// Servomotors stopped
void move_stop(long ms) 
 {
 maneuver=0;
 static int currentSpeed=0;
 long timenow = millis();
 if (maneuver!=maneuverp)
   {
   maneuverp=maneuver;
   currentSpeed=0;   
   }
 while ((millis() - timenow) < ms) 
   {
   MotorL.write(servoL_center);
   MotorR.write(servoR_center);
   }
 //delay(1);
 return;
 } // \move_stop()

 
// Timer1 every 50uS : sends the pulse signal
void timer1_ISR() 
 {
 static volatile int state = 0; // actual state of pulse signal
 static volatile int trigger_time_count = 0; // countdown used to re-triggering

 if (!(--trigger_time_count)) // counting up to 225mS (defined by TICK_COUNTS)
    {
    trigger_time_count = TICK_COUNTS; // reload the counter
    state = 1; // we're ready to retrigger
    }

 switch (state) 
    {
    case 0: // does nothing: I'll wait the 225ms
      break;

    case 1: // send the pulse signal
      digitalWrite(trigPin, HIGH); // trigger pin at high level
      state = 2; // go to the next step, see you in 50uS
      break;

    case 2:  // stop the pulse signal
    default:
      digitalWrite(trigPin, LOW);  // trigger pin at low level
      state = 0;                   // do nothing, see you in 225mS
      break;
    } // \switch state
 } // \timer1_isr()

// interrupt on state change of echo pin
void sonarEcho_ISR() 
 {
 static long echo_start = 0; // time at which echo high pulse is arrived
 static long echo_end = 0; // time at which echo low pulse is arrived
 long echo_duration = 0; // echo lasting in microseconds
 switch (digitalRead(echoPin)) // check echo pin if is high or low
    {
    case HIGH: // echo just started
      echo_end = 0;
      echo_start = micros(); // save start time
      break;

    case LOW: // echo finished
      echo_end = micros(); // save end time
      if (echo_end > echo_start) // I check that there is no micros() overflow
        {
        echo_duration = echo_end - echo_start; // echo lasting, in microseconds
        distance = echo_duration / 58; // distance in cm, global variable
        }
    break;
    } // \switch echo pin
 } // \sonar echo isr

/******************************************************************************************************************
* END Of the file
* 
* if you reached this part, you're a smart person and I want you as follower of my social networks:
* 
* Facebook: https://www.facebook.com/settorezero (Italian language)
* Twitter: https://www.twitter.com/settorezero (English language)
* Instagram - my private profile: https://www.instagram.com/cyb3rn0id (english language)
* Instagram - profile of my blog: https://www.instagram.com/settorezero (italian language)
* Youtube: https://www.youtube.com/settorezero (mainly italian language, but sometimes also English language)
* 
* PLEASE SUBSCRIBE
******************************************************************************************************************/

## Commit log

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2020-08-16 corrected 3d views
    [arlok_3d_exploded.stl, arlok_3d_view.stl]
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2020-09-25 added sound
    used the buzzer on digital pin 8 of MakerUNO
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2020-12-10 Add files via upload
    added stls for female version
    [arlok_eyelashes.stl, arlok_pillar_sonar_rounded.stl]
2020-12-14 added via pixetto support
    [arlok_via_pixetto_support.stl]
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2021-04-23 added an arrow on front part
    [arlok_plate_bottom.stl]
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2021-04-24 corrected plate bottom
    [arlok_plate_bottom.stl]
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2021-05-20 Added STL for printing the o-ring by Raffaello Bonghi
    [arlok_oring.stl]
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2021-06-05 corrected note about power
    is valid for both HC-05 and 06
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2021-06-07 stl files renamed more properly
    [arlok_pillar_hole_(variant_06mm).stl, arlok_pillar_hole_(variant_10mm).stl, arlok_pillar_hole_(variant_12mm).stl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]
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2021-06-11 Added slots for xtal in sonar pillars
    - modified both sonar pillars making a slot for the quartz
    - rear pillar holes "more round"
    [arlok_eyelashes.stl, arlok_pillar_hole_(variant_06mm).stl, arlok_pillar_hole_(variant_10mm).stl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]
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2021-06-23 Added 18650 powering variant
    [arlok_18650_holder.stl]
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2021-06-26 are you tired? print this tyres :D
    [arlok_flat_tyre.stl]
2021-06-26 Changed new parts orientations for easy print, changed names
    [arlok_flat_tyre.stl, arlok_tire_flat.stl, arlok_tire_round.stl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]
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2021-06-27 ops, I did again -> new wheel
    [arlok_wheel_hexagonal.stl]
2021-06-27 Added wheel having honeycomb pattern
    [arlok_wheel_honeycomb.stl]
2021-06-27 honeycomb is now centered
    [arlok_wheel_honeycomb.stl]
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2021-07-08 Added "Feel like a sir" meme moods
    [mood_sir_hat.stl, mood_sir_monocle.stl, mood_sir_moustache.stl]
2021-07-16 New tire: knurled type
    - Added new knurled tire designed by Dario Ciceri
    - Moved Wheels and Tires in their own subfolders in /stl folder
    [arlok_tire_flat.stl, arlok_tire_knurled.stl, arlok_tire_round.stl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]
2021-09-21 added circles and snowflake wheels
    added circles and snowflake wheels
    [arlok_wheel_circles.stl, arlok_wheel_snowflake.stl]
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2021-09-23 moved /stl into /cad
    - /cad folder created for containing both *.stl and *.step files in 2 separate subfolders
    - updated links to stls
    - renamed "wheel" (the first one) in wheel_solid
    - added step file for the solid wheel
    [arlok_18650_holder.stl, arlok_pillar_hole_(variant_06mm).stl, arlok_pillar_hole_(variant_10mm).stl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]
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2023-03-04 Added REV1 Schematic and Gerbers
    [copper_bottom.gbr, copper_top.gbr, drill_1_16.xln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]
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2023-03-05 corrected link to schematic
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2026-05-10 acceleration ramp
    Implemented an acceleration ramp due some servo draw too much current changing direction instantly. Done some other corrections
2026-05-11 moved actual 3dprinted files to v1
    Since I'm working on a v2 release, I moved all stuff to v1 version
    [arlok_18650_holder.stl, arlok_pillar_hole_(variant_06mm).stl, arlok_pillar_hole_(variant_10mm).stl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]
2026-05-11 Added V2 files for 3D printing (preliminary)
    [ArlokV2 - 18650 bracket.step, ArlokV2 - 18650 bracket.stl, ArlokV2 - Backpillar for on-off Rocker 14mm.step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]
2026-05-11 Added 3 "cloved" wheels for V2
    [ArlokV2 Wheel - 3 cloves.step, ArlokV2 Wheel - 3 cloves.stl, ArlokV2 Wheel - 4 cloves.step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]
2026-05-11 Added 6 circles wheel for V2 version
    [ArlokV2 Wheel - 6 circles.step, ArlokV2 Wheel - 6 circles.stl]
2026-05-11 Added TPU Tire for V2
    [ArlokV2 - TPU Tire.step, ArlokV2 - TPU Tire.stl]
2026-05-11 Added Backpillars 6 and 10mmm for V2
    Added V2 backpillars with 6mm hole (for lever switch) and with 10mm hole (for button style switch)
    [ArlokV2 - Backpillar for on-off Lever 6mm.step, ArlokV2 - Backpillar for on-off Lever 6mm.stl, ArlokV2 - Backpillar for on-off button 10mm.step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]
2026-05-11 renamed nut holder files for 18650 V2 bracket
    [ArlokV2 - 18650 bracket nut holder.step, ArlokV2 - 18650 bracket nut holder.stl]
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2026-05-12 Corrected lid
    [ArlokV2 - Caster Hole Lid.step, ArlokV2 - Caster Hole Lid.stl]
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2026-05-13 Corrected caster mounting hole diameter
    [ArlokV2 - Ball Caster Foot.step, ArlokV2 - Ball Caster Foot.stl]
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2026-05-18 Slightly enlarged lower slot hole
    Passed from 3 to 3.8mm so crimping terminal can pass
    [ArlokV2 - Upper Plate.step]
2026-05-18 Added lid for battery display hole
    If you don't want to mount the 1S battery display
    [ArlokV2 - Lid for Battery Display Place.step, ArlokV2 - Lid for Battery Display Place.stl]
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2026-05-25 Step Pedestal has arrow as second shape for giving it a different color
    [ArlokV2 - Pedestal.step, ArlokV2 - Pedestal.stl]
2026-05-25 TP4056 slot, STL with engraved writing
    I bought TP4056 having USB-C and they have a slighly larger PCB so I enllarged the slot by 0.4mm. Modified the STL for having the writing engraved instead of nothing
    [ArlokV2 - Upper Plate.step]
2026-05-26 Added "pois" wheel inspired by Angine De Poitrine
    [ArlokV2 Wheel - 6 circles (pois).step]
2026-05-27 Added a support for 0.96" OLED display
    Put some self-adhesive tape on bottom of the support for attaching it on the PCB
    [ArlokV2 - Oled Support.step, ArlokV2 - Oled Support.stl]
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2026-05-27 Added a tightest version of the hubcap
    central cylinder diameter is 10.8 instead of 10.4 (+0.2mm radius) for a better fit if you printed wheels in PETG
    [ArlokV2 - Hubcap (tight).step, ArlokV2 - Hubcap (tight).stl]
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2026-05-28 Added cad files for attaching printed faces on "Makey" puppet
    [HeadsHuskylens - head.step, HeadsHuskylens - head.stl, HeadsHuskylens - hook.step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]
2026-05-29 added step file: tamiya 70144 ball caster adapter
    [ArlokV2 - Spacer for 70144 Caster.step]
2026-05-29 added stl file: tamiya 70144 ball caster adapter
    [ArlokV2 - Spacer for 70144 Caster.stl]
2026-05-29 Added upper plate having engraved "Arlok2" writing for mono-color printers
    [ArlokV2 - Upper Plate (engraved writing).step]
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
